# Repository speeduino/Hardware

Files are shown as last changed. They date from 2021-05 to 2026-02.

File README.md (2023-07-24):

<div align="center">

Speeduino
 
[]

##### A low cost, DIY friendly Engine Management System (ECU) based on the Arduino framework
</div>

## Speeduino
The Speeduino project is a flexible, fully featured Engine Management Systems (EMS aka ECU) based on the low cost and open source Arduino platform. It provides the hardware, firmware and software components that make up an engine management system, all provided under open licenses. With over 1000 installations, Speeduino has matured into a product that meets the needs of the hobbyist and enthusiast community without driving prices to the levels of traditional aftermarket ECUs.

## Overview
This repositiory contains the official Speeduino hardware designs. All new designs have been made in Kicad, with some early boards developed in Fritzing. 

## License
These designs are release under the [CERN Open Hardware License v2 Strong (CERN-OHL-S)](https://ohwr.org/cern_ohl_s_v2.txt). 
This license is similar to the GPL, however is designed specifically for hardware design files, including PCB layouts and schematics. As the 'strongly reciprocal' version of the CERN OHL is used, you may use, copy, modify and create variations of these designs freely, provided that any changes or variations are also released under this CERN-OHL-S. 

## Where to Buy
[Pre-made Speeduino units/boards are available from a number of official resellers](https://speeduino.com/home/where-to-buy)

These resellers all contribute a portion of sales back to the project to allow for continued development to take place and we encourage sales through them whenever possible. 
 
Of course, being open source, you are free to use the design files provided here to create your own hardware! 

## Support
In addition the manual referenced above, Speeduino has a large and very vibrant community of people to help out with your setup or any questions you might add. 

* [Speeduino Forum](https://speeduino.com/forum) 
* [Discord](hhttps://discord.com/invite/taXeNM6xNb)
* [Facebook](https://www.facebook.com/groups/191918764521976/)

## Contributors

This project exists thanks to all the people who contribute, both in terms of code and testing provided. If you'd like to get involved, please have a read through [Contributing](contributing.md) and then jump on Discord to discuss things further

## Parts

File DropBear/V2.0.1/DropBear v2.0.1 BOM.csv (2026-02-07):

Comment | Designator | Footprint | LCSC
Pololu_Breakout_DRV8825 | A1 | Module:Pololu_Breakout-16_15.2x20.3mm
Battery_Cell | BT1 | Battery:BatteryHolder_Keystone_500
0.1uF | C1,C2,C3,C9,C12,C13,C14,C21,C22,C26,C32,C34,C38 | Capacitor_SMD:C_0805_2012Metric
1uF | C10,C11,C23 | Capacitor_SMD:C_0805_2012Metric
270nF | C15,C19 | Capacitor_SMD:C_0805_2012Metric
0.22uF | C17,C18,C24,C25,C28 | Capacitor_SMD:C_0805_2012Metric
100uF | C27 | Capacitor_SMD:C_1206_3216Metric
100uF | C31 | Capacitor_SMD:CP_Elec_6.3x7.7
47uF | C33,C35 | Capacitor_Tantalum_SMD:CP_EIA-3528-21_Kemet-B
33uF | C36,C37 | Capacitor_SMD:CP_Elec_6.3x7.7
0.33uF | C39 | Capacitor_SMD:C_0805_2012Metric
0.01uF | C4,C7,C20,C29,C30 | Capacitor_SMD:C_0805_2012Metric
4700pF | C5,C16 | Capacitor_SMD:C_0805_2012Metric
1nF | C6,C8 | Capacitor_SMD:C_0805_2012Metric
D_Schottky | D1,D32 | Diode_SMD:D_PowerDI-123
D | D10,D11,D12,D13,D14,D15,D16,D17,D28,D29,D33,D34,D35,D37,D38 | Diode_SMD:D_SOD-323
LED | D2,D3,D4,D5,D6,D7,D8,D9,D18,D19,D20,D21,D22,D23,D24,D25,D31,D36,D41,D42,D43 | LED_SMD:LED_0805_2012Metric
D_TVS | D26,D27 | Diode_SMD:D_SOD-523
D_TVS | D30 | Diode_SMD:D_SOD-123F
D_TVS | D39 | Diode_SMD:D_SMB
D_Schottky | D40 | Diode_SMD:D_SMA_Handsoldering
Polyfuse | F1 | Fuse:Fuse_1812_4532Metric
Polyfuse | F2 | Fuse:Fuse_0603_1608Metric
MAX9926UAEE_V+ | IC1 | Package_SO:QSOP-16_3.9x4.9mm_P0.635mm
ZXMS6006DT8 | IC2,IC3,IC4,IC5 | IC_Automotive:Diodes_SM8
Delphi_Sicma_24 | J1 | Connector_Automotive:Delphi_Sicma_24_Grey
Delphi_Sicma_24 | J2 | Connector_Automotive:Delphi_Sicma_24_Black
EBC05DRXN | J3 | Misc:EBC05DRXN
SolderJumper_2_Bridged | JP1 | Jumper:SolderJumper-2_P1.3mm_Bridged_Pad1.0x1.5mm
Jumper_NO_Small | JP2 | Jumper:SolderJumper-2_P1.3mm_Open_Pad1.0x1.5mm
Jumper_2_Open | JP3,JP4,JP5 | Jumper:SolderJumper-2_P1.3mm_Open_Pad1.0x1.5mm
Q_DUAL_NMOS_S1G1D2S2G2D1 | Q2,Q3 | Package_TO_SOT_SMD:SOT-363_SC-70-6
470R | R1,R31,R33,R34,R38,R39,R44 | Resistor_SMD:R_0805_2012Metric
10k | R19,R20,R64 | Resistor_SMD:R_0805_2012Metric
604R | R29 | Resistor_SMD:R_0805_2012Metric
0R | R3 | Resistor_SMD:R_0805_2012Metric
3.88k | R30 | Resistor_SMD:R_0603_1608Metric_Pad0.98x0.95mm_HandSolder
2.4k | R32 | Resistor_SMD:R_0805_2012Metric
2.49k | R36,R37,R74 | Resistor_SMD:R_0805_2012Metric
120R | R4 | Resistor_SMD:R_0805_2012Metric
180k | R40,R41,R45,R46,R50,R53 | Resistor_SMD:R_0805_2012Metric
348k | R42,R43,R47,R48,R51,R54 | Resistor_SMD:R_0805_2012Metric
1k | R5,R6,R11,R12,R13,R14,R15,R16,R17,R18,R21,R22,R23,R24,R25,R26,R27,R28,R35,R49,R52,R55,R56,R57,R58,R63,R65,R66,R67,R68,R73,R75,R76 | Resistor_SMD:R_0805_2012Metric
100k | R59,R60,R61,R62,R69,R70,R71,R72 | Resistor_SMD:R_0805_2012Metric
10k | R7,R8,R9,R10 | Resistor_SMD:R_1206_3216Metric
SW_DPDT_x2 | SW1,SW2,SW4,SW5 | Misc:AYZ0202AGRLC
SW_DIP_x02 | SW3 | Button_Switch_SMD:SW_DIP_SPSTx02_Slide_9.78x7.26mm_W8.61mm_P2.54mm
Teensy4.1 | U1 | Shields:Teensy41
KP234 | U11 | Misc:KP234
LMV324LIDT | U12,U14 | Package_SO:SOIC-14_3.9x8.7mm_P1.27mm
SP720 | U13 | Package_SO:SOIC-16_3.9x9.9mm_P1.27mm
MC78M05_TO252 | U15 | Package_TO_SOT_SMD:TO-252-2
MCP2562-E-SN | U2 | Package_SO:SOIC-8_3.9x4.9mm_P1.27mm
W25Q32JVSS | U3 | Package_SO:SOIC-8_5.23x5.23mm_P1.27mm
~ | U4 | Misc:ESP32-C3 SUPERMINI
TC4424A | U5,U6,U9,U10 | Package_SO:SOIC-8_3.9x4.9mm_P1.27mm
MC33810 | U7,U8 | IC_Automotive:SOIC32-P0.65-33N

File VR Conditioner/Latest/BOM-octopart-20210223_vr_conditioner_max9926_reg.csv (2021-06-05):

Qty | Line Item | Manufacturer | MPN | Octopart URL | Schematic Reference | Internal Part Number | Description | Lifecycle Status | Lead Time | RoHS | Total Qty (@ Batch Size: 1) | SKU | SKU | SKU | SKU | Packaging | Packaging | Packaging | Packaging | Unit Price (@ Batch Size: 1) | Unit Price (@ Batch Size: 1) | Unit Price (@ Batch Size: 1) | Unit Price (@ Batch Size: 1) | In Stock | In Stock | In Stock | In Stock | MOQ | MOQ | MOQ | MOQ | URL | URL | URL | URL | Distributor [Lowest Price (Overall)] | SKU [Lowest Price (Overall)] | Packaging [Lowest Price (Overall)] | Unit Price (@ Batch Size: 1) [Lowest Price (Overall)] | Line Total [Lowest Price (Overall)] | Batch Total [Lowest Price (Overall)] | In Stock [Lowest Price (Overall)] | MOQ [Lowest Price (Overall)] | URL [Lowest Price (Overall)] | Notes
 |  |  |  |  |  |  |  |  |  |  |  | Digi-Key | Future Electronics | Mouser | RS Components | Digi-Key | Future Electronics | Mouser | RS Components | Digi-Key | Future Electronics | Mouser | RS Components | Digi-Key | Future Electronics | Mouser | RS Components | Digi-Key | Future Electronics | Mouser | RS Components | Digi-Key | Future Electronics | Mouser | RS Components
1 | GRM1857U1A103JA44D | Murata | GRM1857U1A103JA44D | https://octopart.com/grm1857u1a103ja44d-murata-17754272 |  |  |  | Production (Last Updated: 2 weeks ago) | 23w | Compliant | 1 | 490-8269-1-ND | 1117428 | 81-GRM1857U1A103JA4D |  | Cut Tape | Cut Tape | Tape & Reel |  | 0.15622662 | 0.159777225 | 0.17753025 |  | 24842 | 8000 | 6230 |  | 1 | 1 | 1 |  | https://octopart.com/click/track?country=JE&ct=offers&ppid=17754272&sid=459&sig=0a4da8a&vpid=88253296&ai4=706 | https://octopart.com/click/track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 | https://octopart.com/click/track?country=JE&ct=offers&ppid=17754272&sid=2401&sig=0942290&vpid=37708184&ai4=706 |  | Arrow Electronics | GRM1857U1A103JA44D | Cut Tape | 0.1077253557 | 0.1077253557 | 0.1077253557 | 1 | 1 | https://octopart.com/click/track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
2 | CRCW06031K00FKEAHP | Vishay | CRCW06031K00FKEAHP | https://octopart.com/crcw06031k00fkeahp-vishay-42634138 |  |  |  |  | 24w | Compliant | 2 | 541-1.00KSCT-ND | 7110920 | 71-CRCW06031K00FKEAH | 8206776 | Cut Tape | Cut Tape | Tape & Reel |  | 0.12072057000000001 | 0.104387787 | 0.12072057000000001 |  | 205723 | 16210 | 69615 | 2125 | 1 | 1 | 1 | 25 | https://octopart.com/click/track?country=JE&ct=offers&ppid=42634138&sid=459&sig=04dce86&vpid=115677389&ai4=706 | https://octopart.com/click/track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 | https://octopart.com/click/track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 | https://octopart.com/click/track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 | Farnell | 1738905 | Cut Tape | 0.0412 | 0.0824 | 0.0824 | 32145 | 1 | https://octopart.com/click/track?country=JE&ct=offers&ppid=42634138&sid=819&sig=05fe86e&vpid=250080956&ai4=706
4 | CRCW060310K0FKEAHP | Vishay | CRCW060310K0FKEAHP | https://octopart.com/crcw060310k0fkeahp-vishay-42634028 |  |  |  |  | 24w | Compliant | 4 | 541-10.0KSCT-ND | 6103726 | 71-CRCW060310K0FKEAH | 8206742 | Cut Tape | Cut Tape | Tape & Reel |  | 0.12072057000000001 | 0.104387787 | 0.12072057000000001 |  | 84206 | 65036 | 112208 | 2550 | 1 | 1 | 1 | 25 | https://octopart.com/click/track?country=JE&ct=offers&ppid=42634028&sid=459&sig=0828559&vpid=115262443&ai4=706 | https://octopart.com/click/track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 | https://octopart.com/click/track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 | https://octopart.com/click/track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 | Newark | 68R2991 | Cut Tape | 0.017753025000000002 | 0.07101210000000001 | 0.07101210000000001 | 10760 | 1 | https://octopart.com/click/track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
1 | MAX9926UAEE+ | Maxim Integrated | MAX9926UAEE+ | https://octopart.com/max9926uaee%2B-maxim+integrated-42513566 |  |  |  | Production (Last Updated: 1 month ago) | 6w | Compliant | 1 | MAX9926UAEE+-ND | 3086399 | 700-MAX9926UAEE | 1901381 | Tube | Tube | Tube |  | 4.86432885 |  | 6.44789868 | 4.98 | 1069 | 100 | 299 | 0 | 1 | 100 | 1 | 1 | https://octopart.com/click/track?country=JE&ct=offers&ppid=42513566&sid=459&sig=0fd0a9b&vpid=115650128&ai4=706 | https://octopart.com/click/track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 | https://octopart.com/click/track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 | https://octopart.com/click/track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 | Newark | 73Y6635 |  | 4.73650707 | 4.73650707 | 4.73650707 | 10 | 1 | https://octopart.com/click/track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
1 | GCM188R71C105KA64D | Murata | GCM188R71C105KA64D | https://octopart.com/gcm188r71c105ka64d-murata-13159598 |  |  |  | Production (Last Updated: 2 weeks ago) | 27w | Compliant | 1 | 490-5241-1-ND | 7025260 | 81-GCM188R71C105K64D | 7900562 | Cut Tape | Cut Tape | Tape & Reel |  | 0.15622662 | 0.152676015 | 0.15622662 |  | 272359 | 2118 | 0 | 11400 | 1 | 1 | 1 | 25 | https://octopart.com/click/track?country=JE&ct=offers&ppid=13159598&sid=459&sig=065a155&vpid=34232850&ai4=706 | https://octopart.com/click/track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 | https://octopart.com/click/track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 | https://octopart.com/click/track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 | Arrow Electronics | GCM188R71C105KA64D | Cut Tape | 0.1297391067 | 0.1297391067 | 0.1297391067 | 52386 | 1 | https://octopart.com/click/track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
1 | GRM21BR61E106MA73L | Murata | GRM21BR61E106MA73L | https://octopart.com/grm21br61e106ma73l-murata-46693545 |  |  |  | Production (Last Updated: 2 weeks ago) | 29w | Compliant | 1 | 490-10748-1-ND | 3104124 | 81-GRM21BR61E106MA3L | 1726799 | Cut Tape | Cut Tape | Tape & Reel |  | 0.17753025 | 0.173979645 | 0.18463146 |  | 169134 | 22568 | 63443 | 700 | 1 | 1 | 1 | 50 | https://octopart.com/click/track?country=JE&ct=offers&ppid=46693545&sid=459&sig=0e7381d&vpid=210890997&ai4=706 | https://octopart.com/click/track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 | https://octopart.com/click/track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 | https://octopart.com/click/track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 | Arrow Electronics | GRM21BR61E106MA73L | Cut Tape | 0.1290289857 | 0.1290289857 | 0.1290289857 | 18282 | 1 | https://octopart.com/click/track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
2 | GRM1885C1H102JA01D | Murata | GRM1885C1H102JA01D | https://octopart.com/grm1885c1h102ja01d-murata-196169 |  |  |  | Production (Last Updated: 2 weeks ago) | 29w | Compliant | 2 | 490-1451-1-ND | 5104092 | 81-GRM39C102J50 | 7235795 | Cut Tape | Cut Tape | Tape & Reel |  | 0.07101210000000001 | 0.0102257424 | 0.07101210000000001 |  | 0 | 2890 | 845260 | 5800 | 1 | 1 | 1 | 200 | https://octopart.com/click/track?c=1&country=JE&ct=offers&ppid=196169&sid=459&sig=0c67cea&vpid=1086114&ai4=706 | https://octopart.com/click/track?country=JE&ct=offers&ppid=196169&sid=2454&sig=06c4930&vpid=495870445&ai4=706 | https://octopart.com/click/track?country=JE&ct=offers&ppid=196169&sid=2401&sig=0c58fdf&vpid=37712468&ai4=706 | https://octopart.com/click/track?country=JE&ct=offers&ppid=196169&sid=10022&sig=0888f0c&vpid=199072014&ai4=706 | Future Electronics | 5104092 | Cut Tape | 0.0102257424 | 0.0204514848 | 0.0204514848 | 2890 | 1 | https://octopart.com/click/track?country=JE&ct=offers&ppid=196169&sid=2454&sig=06c4930&vpid=495870445&ai4=706
1 | GCJ188R71C104KA01D | Murata | GCJ188R71C104KA01D | https://octopart.com/gcj188r71c104ka01d-murata-21222040 |  |  |  | Production (Last Updated: 2 weeks ago) | 27w | Compliant | 1 | 490-5796-1-ND | 6113232 | 81-GCJ188R71C104KA1D |  | Cut Tape | Cut Tape | Tape & Reel |  | 0.19173267000000002 | 0.188182065 | 0.17042904 |  | 38484 | 1000 | 178383 |  | 1 | 1 | 1 |  | https://octopart.com/click/track?country=JE&ct=offers&ppid=21222040&sid=459&sig=0e464ea&vpid=44469513&ai4=706 | https://octopart.com/click/track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 | https://octopart.com/click/track?country=JE&ct=offers&ppid=21222040&sid=2401&sig=02bb046&vpid=47654983&ai4=706 |  | Mouser | 81-GCJ188R71C104KA1D | Tape & Reel | 0.17042904 | 0.17042904 | 0.17042904 | 178383 | 1 | https://octopart.com/click/track?country=JE&ct=offers&ppid=21222040&sid=2401&sig=02bb046&vpid=47654983&ai4=706

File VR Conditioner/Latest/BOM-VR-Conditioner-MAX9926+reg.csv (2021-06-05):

Reference | Value | Footprint | Datasheet | Critical | Description | MFG Name | MFG Part Num | Package JEDEC ID
FID1 | Fiducial | Fiducial:Fiducial_0.5mm_Mask1mm | ~
FID2 | Fiducial | Fiducial:Fiducial_0.5mm_Mask1mm | ~
U1 | MAX9926UAEE+ | MAX9926UAEE+:MAX9926UAEE&plus_ | https://datasheet.octopart.com/MAX9926UAEE%2B-Maxim-Integrated-datasheet-11046290.pdf | Yes | MAX9926 Series 10 mA Differential Input Logic Output Sensor Interface -SSOP-16 | Maxim Integrated | MAX9926UAEE+ | SSOP-16
C1 | 10n | Capacitor_SMD:C_0603_1608Metric | ~ |  | 10 V ±5% Tolerance U2J Multilayer Ceramic Capacitor | Murata Murata | GRM1857U1A103JA44D | 0603_1608Metric
C2 | 100n | Capacitor_SMD:C_0603_1608Metric | ~ |  | Ceramic 0.1uF 16V X7R 10% Pad SMD 0603 Soft Termination 125C Automotive T/R | Murata | GCJ188R71C104KA01D | 0603_1608Metric
C3 | 1u | Capacitor_SMD:C_0603_1608Metric | ~ |  | 16V ±10% Tolerance X7R Surface Mount Multilayer Ceramic Capacitor | Murata | GCM188R71C105KA64D | 0603_1608Metric
C20 | 1n | Capacitor_SMD:C_0603_1608Metric | ~ |  | 1000 pF 50 V ±5 % Tolerance C0G SMT Multilayer Ceramic Capacitor | Murata | GRM1885C1H102JA01D | 0603_1608Metric
C10 | 1n | Capacitor_SMD:C_0603_1608Metric | ~ |  | 1000 pF 50 V ±5 % Tolerance C0G SMT Multilayer Ceramic Capacitor | Murata | GRM1885C1H102JA01D | 0603_1608Metric
R22 | 10k | Resistor_SMD:R_0603_1608Metric_Pad1.05x0.95mm_HandSolder | ~ |  |  | Yageo | RC1206FR-7W10KL | Resistor_SMD:R_1206_3216Metric
R21 | 10k | Resistor_SMD:R_0603_1608Metric_Pad1.05x0.95mm_HandSolder | ~ |  |  | Yageo | RC1206FR-7W10KL | Resistor_SMD:R_1206_3216Metric
R11 | 10k | Resistor_SMD:R_0603_1608Metric_Pad1.05x0.95mm_HandSolder | ~ |  |  | Yageo | RC1206FR-7W10KL | Resistor_SMD:R_1206_3216Metric
R12 | 10k | Resistor_SMD:R_0603_1608Metric_Pad1.05x0.95mm_HandSolder | ~ |  |  | Yageo | RC1206FR-7W10KL | Resistor_SMD:R_1206_3216Metric
R13 | 4.7k | Resistor_THT:R_Axial_DIN0207_L6.3mm_D2.5mm_P7.62mm_Horizontal | ~ | DoNoPlace. User option | 3W, 5%
J1 | 8-pin header | Package_DIP:DIP-8_W7.62mm | ~
R20 | 1k | Resistor_SMD:R_0603_1608Metric_Pad1.05x0.95mm_HandSolder | ~ |  | Thick Film; +/-1% 0.2W | Vishay | CRCW06031K00FKEAHP | 0603_1608Metric
R10 | 1k | Resistor_SMD:R_0603_1608Metric_Pad1.05x0.95mm_HandSolder | ~ |  | Thick Film; +/-1% 0.2W | Vishay | CRCW06031K00FKEAHP | 0603_1608Metric
H1 | MountingHole | MountingHole:MountingHole_2.2mm_M2 | ~
H2 | MountingHole | MountingHole:MountingHole_2.2mm_M2 | ~
C4 | 10u | Capacitor_SMD:C_0805_2012Metric | ~ |  | 25 V 10 uF ±20% Tolerance X5R Multilayer Ceramic Capacitor | Murata | GRM21BR61E106MA73L | 0805_2012Metric
R23 | 4.7k | Resistor_THT:R_Axial_DIN0207_L6.3mm_D2.5mm_P7.62mm_Horizontal | ~ | DoNoPlace. User option | 3W, 5%
U2 | AMS1117CD-5.0 | Package_TO_SOT_THT:TO-92_Inline_Wide | http://www.advanced-monolithic.com/pdf/ds1117.pdf | DoNoPlace. User option | 1A Low Dropout Voltage Regulator | Advanced Monolithic Systems | AMS1117-5.0 | TO92 inline wide
J2 | Edge | Connector_PinHeader_2.54mm:PinHeader_1x04_P2.54mm_Horizontal | ~ | DoNoPlace. User option

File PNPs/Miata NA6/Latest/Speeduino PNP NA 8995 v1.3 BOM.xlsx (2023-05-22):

Reference | Quantity | Value | Footprint | Manufacturer_Name | Manufacturer_Part_Number | URL | Digikey Part Number
C1 C29 | 2 | 0.01uF | Capacitor_SMD:C_0805_2012Metric | Yageo | CC0805KRX7R9BB103 | https://www.digikey.com/product-detail/en/yageo/CC0805KRX7R9BB103/311-1136-1-ND/303046 | 311-1136-1-ND
C17 | 1 | 22uF | Capacitor_SMD:CP_Elec_4x5.8 | Panasonic | EEE-FK0J220R | https://www.digikey.com/product-detail/en/panasonic-electronic-components/EEE-FK0J220R/PCE3765CT-ND/766141 | PCE3765CT-ND
C19 | 1 | 10uF | Capacitor_Tantalum_SMD:CP_EIA-7343-31_Kemet-D | Kemet | T491D106K050AT | https://www.digikey.com/product-detail/en/kemet/T491D106K050AT/399-8361-1-ND/3472084 | 399-8361-1-ND
C2 C30 C18 | 3 | 1uF | Capacitor_SMD:C_0805_2012Metric | Yageo | CC0805KKX7R7BB105 | https://www.digikey.com/product-detail/en/yageo/CC0805KKX7R7BB105/311-1365-1-ND/2103149 | 311-1365-1-ND
C20 C22 C23 | 3 | 0.1uF | Capacitor_SMD:C_1206_3216Metric | Kemet | C1206C104K5RAC7867 | https://www.digikey.com/product-detail/en/kemet/C1206C104K5RAC7867/399-1249-1-ND/411524 | 399-1249-1-ND
C21 | 1 | 22uF | Capacitor_SMD:C_0805_2012Metric_Pad1.15x1.40mm_HandSolder | Samsung | CL21A226KQCLRNC | https://www.digikey.com.au/product-detail/en/samsung-electro-mechanics/CL21A226KQCLRNC/1276-6687-1-ND/5961546 | 1276-6687-1-ND
C24 C25 | 2 | 47uF | Capacitor_Tantalum_SMD:CP_EIA-3528-21_Kemet-B | AVX | TAJB476K006RNJ | https://www.digikey.com/product-detail/en/avx-corporation/TAJB476K006RNJ/478-1692-1-ND/564724 | 478-1692-1-ND
C32 | 1 | 0.1uF | Capacitor_SMD:C_0805_2012Metric_Pad1.15x1.40mm_HandSolder | Yageo | CC0805KRX7R9BB104 | https://www.digikey.com.au/product-detail/en/yageo/CC0805KRX7R9BB104/311-1140-1-ND/303050 | 311-1140-1-ND
C33 C3 C9 C10 C11 C4 C15 C16 C31 C27 C26 C28 | 12 | 0.1uF | Capacitor_SMD:C_0805_2012Metric | Yageo | CC0805KRX7R9BB104 | https://www.digikey.com.au/product-detail/en/yageo/CC0805KRX7R9BB104/311-1140-1-ND/303050 | 311-1140-1-ND
C5 | 1 | 0.27uF | Capacitor_SMD:C_0805_2012Metric | Yageo | CC0805JRX7R7BB274 | https://www.digikey.com.au/product-detail/en/yageo/CC0805JRX7R7BB274/311-4268-1-ND/8025357 | 311-4268-1-ND
C6 C12 C13 C14 C7 | 5 | 0.22uF | Capacitor_SMD:C_0805_2012Metric | Samsung | CL21B224KOCNNNC | https://www.digikey.com/product-detail/en/samsung-electro-mechanics-america-inc/CL21B224KOCNNNC/1276-1284-1-ND/3889370 | 1276-1284-1-ND
C8 | 1 | 470pf | Capacitor_SMD:C_0805_2012Metric | Yageo | CC0805KRX7R9BB471 | https://www.digikey.com/product-detail/en/yageo/CC0805KRX7R9BB471/311-1124-1-ND/303034 | 311-1124-1-ND
D10 D9 D5 D6 D20 | 5 | D | Diode_SMD:D_SOD-323 | Micro Commercial Co | 1N4448WX-TP | https://www.digikey.com/product-detail/en/micro-commercial-co/1N4448WX-TP/1N4448WXTPMSCT-ND/789338 | 1N4448WXTPMSCT-ND
D12 | 1 | D_Schottky | Diode_THT:D_DO-41_SOD81_P7.62mm_Horizontal | Micro Commercial Co | 1N5818-TP | https://www.digikey.com/product-detail/en/micro-commercial-co/1N5818-TP/1N5818-TPCT-ND/950587 | 1N5818-TPCT-ND
D16 D15 D17 | 3 | D | Diode_SMD:D_SMB | ON Semi | NBRS2H100T3G | https://www.digikey.com/en/products/detail/on-semiconductor/NBRS2H100T3G/1792405 | NBRS2H100T3GTR-ND
D22 D21 | 2 | LED_Green | LED_SMD:LED_0805_2012Metric | Osram | LG R971-KN-1 | https://www.digikey.com/product-detail/en/osram-opto-semiconductors-inc/LG-R971-KN-1/475-1410-1-ND/1802598 | 475-1410-1-ND
D23 | 1 | D_TVS | Diode_SMD:D_SMB | Bournes Inc. | SMBJ40A-Q | https://www.digikey.com.au/product-detail/en/bourns-inc/SMBJ40A-Q/SMBJ40A-QCT-ND/10222718 | SMBJ40A-QCT-ND
D4 D3 D8 D7 D1 D2 D11 D19 D18 | 9 | LED | LED_SMD:LED_0805_2012Metric | Osram | LH R974-LP-1 | https://www.digikey.com/product-detail/en/osram-opto-semiconductors-inc/LH-R974-LP-1/475-1415-1-ND/1802604 | 475-1415-1-ND
F1 | 1 | Polyfuse | Fuse:Fuse_0603_1608Metric | Bel Fuse | 0ZCM0008FF2G | https://www.digikey.com.au/product-detail/en/bel-fuse-inc/0ZCM0008FF2G/507-1817-1-ND/4156262 | 507-1817-1-ND
J1 | 1 | 174917-1 | Connector_Automotive:1749171 | TE Connectivity | 174917-1
Q1 | 1 | Q_PNP_BCEC | Package_TO_SOT_SMD:SOT-223-3_TabPin2 | Diodes Inc | FZT753TA | https://www.digikey.com.au/product-detail/en/diodes-incorporated/FZT753TA/FZT753CT-ND/92847 | FZT753CT-ND
R1 R2 R15 R16 R3 R4 R56 R57 R42 R41 R51 R50 R47 | 13 | 100k | Resistor_SMD:R_0805_2012Metric_Pad1.15x1.40mm_HandSolder | Yageo | RC0805FR-07100KL | https://www.digikey.com/product-detail/en/yageo/RC0805FR-07100KL/311-100KCRCT-ND/730491 | 311-100KCRCT-ND
R10 R9 R20 R19 R11 R12 R60 R61 R25 | 9 | 2.4k | Resistor_SMD:R_0805_2012Metric | Yageo | RC0805FR-072K4L | https://www.digikey.com/product-detail/en/yageo/RC0805FR-072K4L/311-2.40KCRCT-ND/730637 | 311-2.40KCRCT-ND
R22 | 1 | 3.9k | Resistor_SMD:R_0805_2012Metric | Yageo | RC0805FR-073K9L | https://www.digikey.com/product-detail/en/yageo/RC0805FR-073K9L/311-3.90KCRCT-ND/730785 | 311-3.90KCRCT-ND
R26 R23 R30 R31 R32 R24 R66 R65 R55 R54 | 10 | 470R | Resistor_SMD:R_0805_2012Metric | Panasonic | ERJ-6ENF4700V | https://www.digikey.com/product-detail/en/panasonic-electronic-components/ERJ-6ENF4700V/P470CCT-ND/1746871 | P470CCT-ND
R27 R28 R52 | 3 | 2.49k | Resistor_SMD:R_0805_2012Metric | Yageo | RT0805BRD072K49L | https://www.digikey.com/product-detail/en/yageo/RT0805BRD072K49L/YAG1854CT-ND/5139302 | YAG1854CT-ND
R35 R36 | 2 | 220R | Resistor_SMD:R_0805_2012Metric_Pad1.15x1.40mm_HandSolder | Yageo | RC0805FR-07220RL | https://www.digikey.com/product-detail/en/yageo/RC0805FR-07220RL/311-220CRCT-ND/730688 | 311-220CRCT-ND
R37 | 1 | 10k | Resistor_SMD:R_0805_2012Metric | Yageo | RC0805JR-0710KL | https://www.digikey.com/product-detail/en/yageo/RC0805JR-0710KL/311-10KARCT-ND/731188 | 311-10KARCT-ND
R38 | 1 | 120R | Resistor_SMD:R_0805_2012Metric | Yageo | RC0805FR-07120RL | https://www.digikey.com/product-detail/en/yageo/RC0805FR-07120RL/311-120CRCT-ND/730522 | 311-120CRCT-ND
R43 | 1 | 2k | Resistor_SMD:R_0805_2012Metric_Pad1.15x1.40mm_HandSolder | Yageo | RC0805FR-072KL | https://www.digikey.com/product-detail/en/yageo/RC0805FR-072KL/311-2.00KCRCT-ND/730611 | 311-2.00KCRCT-ND
R46 | 1 | 10k | Resistor_SMD:R_0805_2012Metric_Pad1.15x1.40mm_HandSolder | Yageo | RC0805JR-0710KL |  | 311-10KARCT-ND
R5 R6 R17 R18 R7 R8 R58 R59 R21 R29 R33 R34 R39 R40 R48 R49 R44 R45 R53 R64 | 20 | 1k | Resistor_SMD:R_0805_2012Metric_Pad1.15x1.40mm_HandSolder | Yageo | RC0805FR-071KL | https://www.digikey.com/product-detail/en/yageo/RC0805FR-071KL/311-1.00KCRCT-ND/730391 | 311-1.00KCRCT-ND
R67 | 1 | 22K | Resistor_SMD:R_0805_2012Metric | Yageo | AC0805JR-0722KL | https://www.digikey.com.au/product-detail/en/yageo/AC0805JR-0722KL/YAG3773CT-ND/6006622 | YAG3773CT-ND
RV1 | 1 | Varistor | Varistor:RV_Disc_D15.5mm_W4.7mm_P7.5mm | Bourns Inc | MOV-14D220K | https://www.digikey.com.au/product-detail/en/bourns-inc/MOV-14D220K/MOV-14D220K-ND/2799109 | MOV-14D220K-ND
S1 | 1 | AYZ0202AGRLC | AYZ0202AGRLC | C & K COMPONENTS | AYZ0202AGRLC | https://www.digikey.com.au/product-detail/en/c-k/AYZ0202AGRLC/401-2013-1-ND/1640122 | 401-2013-1-ND
U1 | 1 | MC33814 | Package_QFP:LQFP-48-1EP_7x7mm_P0.5mm_EP3.6x3.6mm_ThermalVias | NCP | MC33814 | http://au.element14.com/nxp/mc33814ae/ic-control-1-cylinder-engine-48lqfp/dp/2311285
U11 | 1 | KP234 | Misc:KP234 | Infineon | KP234XTMA1 | https://www.digikey.com.au/product-detail/en/infineon-technologies/KP234XTMA1/448-KP234XTMA1CT-ND/12718428 | 448-KP234XTMA1CT-ND
U2 U4 U7 U9 | 4 | VNLD5090 | Package_SO:SO-8_3.9x4.9mm_P1.27mm | STMicro | VNLD5090-E | https://mouser.com/search/ProductDetail.aspx?R=0virtualkey0virtualkeyVNLD5090-E | 497-18682-ND
U3 U10 | 2 | TC4424A | Package_SO:SOIC-8_3.9x4.9mm_P1.27mm | Microchip | TC4424AVOA | https://www.digikey.com/product-detail/en/microchip-technology/TC4424AVOA/TC4424AVOA-ND/1098908 | TC4424AVOA-ND
U5 | 1 | MPX4250 | Misc:MPX4250 | NXP | MPX4250AP | https://www.digikey.com.au/product-detail/en/nxp-usa-inc/MPX4250AP/MPX4250AP-ND/464053 | MPX4250AP-ND
U6 | 1 | SP720 | Package_SO:SOIC-16_3.9x9.9mm_P1.27mm | Littelfuse | SP720ABTG | https://www.digikey.com/product-detail/en/littelfuse-inc/SP720ABTG/F3162CT-ND/1984458 | F3162CT-ND
U8 | 1 | VN5160S-E | Package_SO:SO-8_3.9x4.9mm_P1.27mm | STMicro | VN5160S-E | https://www.digikey.com.au/products/en?keywords=VN5160S-E | 497-19720-ND
XA1 | 4 | Arduino_Mega2560 header pins | CONN HEADER .100" SNGL STR 40POS | Sullins Connector Solutions | PREC040SAAN-RC | https://www.digikey.com.au/products/en?keywords=S1012EC-40-ND |  | Pins attach to bottom of board

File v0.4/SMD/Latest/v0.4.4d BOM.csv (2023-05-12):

Reference | Quantity | Value | Footprint | Manufacturer_Name | Manufacturer_Part_Number | URL | Part # | Voltage | Allied_Number | Description | RS Part Number | RS Price/Stock | TR PN | Tube PN | Spice_Model | Spice_Netlist_Enabled | Spice_Primitive
C1 C15 | 2 | 0.01uF | Capacitor_SMD:C_0805_2012Metric | Yageo | CC0805KRX7R9BB103 | https://www.digikey.com/product-detail/en/yageo/CC0805KRX7R9BB103/311-1136-1-ND/303046
C17 | 1 | 10uF | Capacitor_Tantalum_SMD:CP_EIA-7343-31_Kemet-D | Kemet | T491D106K050AT | https://www.digikey.com/product-detail/en/kemet/T491D106K050AT/399-8361-1-ND/3472084 |  | 35v
C19 | 1 | 22uF | Capacitor_SMD:C_0805_2012Metric_Pad1.15x1.40mm_HandSolder | Samsung | CL21A226KQCLRNC | https://www.digikey.com.au/product-detail/en/samsung-electro-mechanics/CL21A226KQCLRNC/1276-6687-1-ND/5961546
C21 | 1 | 47uF | Capacitor_Tantalum_SMD:CP_EIA-3528-21_Kemet-B | AVX | TAJB476K006RNJ | https://www.digikey.com/product-detail/en/avx-corporation/TAJB476K006RNJ/478-1692-1-ND/564724 |  | 10v
C24 C26 C3 C9 C10 C11 C4 C16 C18 C20 C23 C22 C28 | 13 | 0.1uF | Capacitor_SMD:C_0805_2012Metric | Yageo | CC0805KRX7R9BB104 | https://www.digikey.com.au/product-detail/en/yageo/CC0805KRX7R9BB104/311-1140-1-ND/303050
C25 C27 C2 | 3 | 1uF | Capacitor_SMD:C_0805_2012Metric | Yageo | CC0805KKX7R7BB105 | https://www.digikey.com/product-detail/en/yageo/CC0805KKX7R7BB105/311-1365-1-ND/2103149
C6 C12 C13 C14 C7 C5 | 6 | 0.22uF | Capacitor_SMD:C_0805_2012Metric | Samsung | CL21B224KOCNNNC | https://www.digikey.com/product-detail/en/samsung-electro-mechanics-america-inc/CL21B224KOCNNNC/1276-1284-1-ND/3889370
C8 C29 | 2 | 470pf | Capacitor_SMD:C_0805_2012Metric | Yageo | CC0805KRX7R9BB471 | https://www.digikey.com/product-detail/en/yageo/CC0805KRX7R9BB471/311-1124-1-ND/303034
D12 D11 D5 D6 | 4 | D | Diode_SMD:D_SOD-323 | MCC | 1N4448WX-TP | https://www.digikey.com/product-detail/en/micro-commercial-co/1N4448WX-TP/1N4448WXTPMSCT-ND/789338
D13 D20 | 2 | D_Zener | Diode_SMD:D_SOD-323 | On Semi | MM3Z5V1ST1G | https://www.digikey.com/product-detail/en/on-semiconductor/MM3Z5V1ST1G/MM3Z5V1ST1GOSCT-ND/964547 | MM3Z5V1ST1G
D14 | 1 | B130-13-F | Diode_SMD:D_SMA | Diodes Inc | B130-13-F | https://www.digikey.com.au/product-detail/en/diodes-incorporated/B130-13-F/B130-FDICT-ND/815318
D15 | 1 | D_TVS | Diode_SMD:D_SMB | Bournes Inc. | SMBJ40A-Q | https://www.digikey.com.au/product-detail/en/bourns-inc/SMBJ40A-Q/SMBJ40A-QCT-ND/10222718
D19 D16 D17 D18 | 4 | D | Diode_SMD:D_SOD-123F | ONSEMI | S110FA | https://www.digikey.com/en/products/detail/on-semiconductor/S110FA/5892098
D4 D3 D8 D7 D1 D2 D9 D10 | 8 | LED | LED_SMD:LED_0805_2012Metric | Osram | LH R974-LP-1 | https://www.digikey.com/product-detail/en/osram-opto-semiconductors-inc/LH-R974-LP-1/475-1415-1-ND/1802604
F1 F2 | 2 | Polyfuse | Fuse:Fuse_1812_4532Metric | Bel Fuse | 0ZCC0050FF2C | https://www.digikey.com.au/product-detail/en/bel-fuse-inc/0ZCC0050FF2C/507-1361-1-ND/1560228
IC3 | 2 | Trig Cond Socket | Package_DIP:DIP-8_W7.62mm_Socket | Sullins Connector Solutions | PPTC041LFBN-RC | https://www.digikey.com.au/product-detail/en/sullins-connector-solutions/PPTC041LFBN-RC/S7002-ND/810144
J3 | 1 | Conn_01x02 | TerminalBlock_Phoenix:TerminalBlock_Phoenix_PT-1,5-2-5.0-H_1x02_P5.00mm_Horizontal | TE | 282836-2 | https://www.digikey.com.au/product-detail/en/te-connectivity-amp-connectors/282836-2/A98076-ND/1826939
J4 | 1 | Conn_02x20_Counter_Clockwise | Connector_IDC:IDC-Header_2x20_P2.54mm_Vertical | CNC Tech | 571-5103308-8 | https://www.digikey.com.au/products/en?keywords=1175-1614-ND
JP1 | 1 | Ignition Voltage | Connector_PinHeader_2.54mm:PinHeader_1x03_P2.54mm_Vertical | Harwin Inc | M20-9990345 | https://www.digikey.com.au/products/en?keywords=M20-9990345
JP2 JP3 | 2 | VR-HALL | Connector_PinHeader_2.54mm:PinHeader_1x03_P2.54mm_Vertical | Harwin Inc | M20-9990345 | https://www.digikey.com.au/products/en?keywords=M20-9990345
JP5 JP4 | 2 | PULL-UP | Connector_PinHeader_2.54mm:PinHeader_1x02_P2.54mm_Vertical | Harwin Inc | M20-9990245 | https://www.digikey.com.au/products/en?keywords=M20-9990245
Q1 Q3 Q2 | 3 | SSM3K357R | Package_TO_SOT_SMD:SOT-23 | Toshiba | SSM3K357R | https://www.digikey.com.au/product-detail/en/toshiba-semiconductor-and-storage/SSM3K357RLF/SSM3K357RLFCT-ND/8611183
R1 R2 R15 R16 R3 R4 R19 R20 R50 R49 R61 R60 | 12 | 100k | Resistor_SMD:R_0805_2012Metric | Yageo | RC0805FR-07100KL | https://www.digikey.com/product-detail/en/yageo/RC0805FR-07100KL/311-100KCRCT-ND/730491
R10 R9 R24 R23 R11 R12 R25 R26 R33 | 9 | 2.4k | Resistor_SMD:R_0805_2012Metric | Yageo | RC0805FR-072K4L | https://www.digikey.com/product-detail/en/yageo/RC0805FR-072K4L/311-2.40KCRCT-ND/730637
R27 R28 R13 R14 | 4 | 10R | Resistor_SMD:R_1206_3216Metric | Yageo | RC1206FR-0710RL | https://www.digikey.com/en/products/detail/yageo/RC1206FR-0710RL/728482
R30 | 1 | 3.9k | Resistor_SMD:R_0805_2012Metric | Yageo | RC0805FR-073K9L | https://www.digikey.com/product-detail/en/yageo/RC0805FR-073K9L/311-3.90KCRCT-ND/730785
R34 R31 R38 R39 R40 R32 R55 R63 R62 | 9 | 470R | Resistor_SMD:R_0805_2012Metric | Panasonic | ERJ-6ENF4700V | https://www.digikey.com/product-detail/en/panasonic-electronic-components/ERJ-6ENF4700V/P470CCT-ND/1746871
R35 R36 | 2 | 2.49k | Resistor_SMD:R_0805_2012Metric | Yageo | RT0805BRD072K49L | https://www.digikey.com/product-detail/en/yageo/RT0805BRD072K49L/YAG1854CT-ND/5139302
R43 R44 | 2 | 220R | Resistor_SMD:R_0805_2012Metric | Yageo | RC0805FR-07220RL | https://www.digikey.com/product-detail/en/yageo/RC0805FR-07220RL/311-220CRCT-ND/730688
R45 R51 | 2 | 10k | Resistor_SMD:R_0805_2012Metric | Yageo | RC0805JR-0710KL | https://www.digikey.com/product-detail/en/yageo/RC0805JR-0710KL/311-10KARCT-ND/731188
R46 | 1 | 120R | Resistor_SMD:R_0805_2012Metric | Yageo | RC0805FR-07120RL | https://www.digikey.com/product-detail/en/yageo/RC0805FR-07120RL/311-120CRCT-ND/730522
R5 R6 R17 R18 R7 R8 R21 R22 R29 R37 R41 R42 R47 R48 R56 R57 R53 R54 | 18 | 1k | Resistor_SMD:R_0805_2012Metric | Yageo | RC0805FR-071KL | https://www.digikey.com/product-detail/en/yageo/RC0805FR-071KL/311-1.00KCRCT-ND/730391
R52 | 1 | 2k | Resistor_SMD:R_0805_2012Metric | Yageo | RC0805FR-072KL | https://www.digikey.com/product-detail/en/yageo/RC0805FR-072KL/311-2.00KCRCT-ND/730611
S1 | 1 | AYZ0202AGRLC | Misc:AYZ0202AGRLC | C & K COMPONENTS | AYZ0202AGRLC | https://www.digikey.com.au/product-detail/en/c-k/AYZ0202AGRLC/401-2013-1-ND/1640122 |  |  | 70417470 | AYZ0202AGRLC (Slide Switches) | 7931504P | http://uk.rs-online.com/web/p/products/7931504P
U1 U3 U7 U9 | 4 | VNLD5090 | Package_SO:SOIC-8_3.9x4.9mm_P1.27mm | STMicro | VNLD5090-E | https://www.digikey.com.au/products/en?keywords=VNLD5090-E
U2 U4 | 2 | IXDN602 | Package_SO:SOIC-8_3.9x4.9mm_P1.27mm | IXYS | IXDN602SIATR | https://www.digikey.com/en/products/detail/ixys-integrated-circuits-division/IXDN602SIATR/2424695
U5 | 1 | MPX4250 | Misc:MPX4250 | NXP | MPX4250AP | https://www.digikey.com.au/product-detail/en/nxp-usa-inc/MPX4250AP/MPX4250AP-ND/464053
U6 | 1 | SP720 | Package_SO:SOIC-16_3.9x9.9mm_P1.27mm | Littelfuse | SP720ABTG | https://www.digikey.com/product-detail/en/littelfuse-inc/SP720ABTG/F3162CT-ND/1984458
U8 | 1 | LM2940S-5.0/NOPB | Package_TO_SOT_SMD:TO-263-3_TabPin2 | TI | LM2940S-5.0/NOPB | https://www.digikey.com.au/products/en?keywords=LM2940S-5.0%2FNOPB |  |  |  |  |  |  | LM2940SX-5.0/NOPB | LM2940S-5.0/NOPB
XA1 | 4 | Arduino_Mega2560 header pins | CONN HEADER .100" SNGL STR 40POS | Sullins Connector Solutions | PREC040SAAN-RC | https://www.digikey.com.au/products/en?keywords=S1012EC-40-ND | Pins on underside of board

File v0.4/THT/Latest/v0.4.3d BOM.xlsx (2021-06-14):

 | Speeduino BOM |  |  | v0.4.3d
Reference | Quantity | Value | Manufacturer_Name | Manufacturer_Part_Number | Footprint | URL | Digikey Part Number | Digikey BOM import
A1 | 2 | DRV8825 socket | Sullins | PPTC081LFBN-RC | Module:Pololu_Breakout-16_15.2x20.3mm | https://www.digikey.com.au/products/en?keywords=PPTC081LFBN-RC | S7006-ND | 2,S7006-ND
C1 C15 | 2 | 0.01uF | TDK | FA18X7R1H103KNU06 | Capacitor_THT:C_Disc_D5.0mm_W2.5mm_P2.50mm | https://www.digikey.com.au/product-detail/en/tdk-corporation/FA18X7R1H103KNU06/445-174244-1-ND/5865002 | 445-174244-1-ND | 2,445-174244-1-ND
C17 | 1 | 10uF | Panasonic | EEU-FC1H100L | Capacitor_THT:CP_Radial_D5.0mm_P2.00mm | https://www.digikey.com.au/product-detail/en/panasonic-electronic-components/EEU-FC1H100L/P10316-ND/266325 | P10316-ND | 1,P10316-ND
C19 | 1 | 22uF | TDK | FA22X7R1E226MRU06 | Capacitor_THT:C_Disc_D7.5mm_W5.0mm_P5.00mm |  | 445-180603-1-ND | 1,445-180603-1-ND
C21 | 1 | 47uF | Panasonic | EEU-FC1H470B | Capacitor_THT:CP_Radial_D8.0mm_P5.00mm |  | P19658CT-ND | 1,P19658CT-ND
C3 C4 C9 C10 C11 C16 C18 C20 C22 C23 C24 C28 | 12 | 0.1uF | TDK | FA18X8R1E104KNU06 | Capacitor_THT:C_Disc_D5.0mm_W2.5mm_P2.50mm | https://www.digikey.com.au/product-detail/en/tdk-corporation/FA18X8R1E104KNU06/445-180563-1-ND/9560689 | 445-180563-1-ND | 12,445-180563-1-ND
C2 C25 | 2 | 1uF | TDK | FA18X7R1E105KRU06 | Capacitor_THT:C_Disc_D5.0mm_W2.5mm_P2.50mm | https://www.digikey.com.au/product-detail/en/tdk-corporation/FA18X7R1E105KRU06/445-180543-1-ND/9560669 | 445-180543-1-ND | 2,445-180543-1-ND
C5 C6 C7 C12 C13 C14 | 6 | 0.22uF | TDK | FA18X8R1E224KRU06 | Capacitor_THT:C_Disc_D5.0mm_W2.5mm_P2.50mm | https://www.digikey.com.au/product-detail/en/tdk-corporation/FA18X8R1E224KRU06/445-180564-1-ND/9560690 | 445-180564-1-ND | 6,445-180564-1-ND
C8 C29 | 2 | 470pf | TDK | FA18NP01H471JNU06 | Capacitor_THT:C_Disc_D5.0mm_W2.5mm_P2.50mm | https://www.digikey.com.au/product-detail/en/tdk-corporation/FA18NP01H471JNU06/445-180522-1-ND/9560648 | 445-180522-1-ND | 2,445-180522-1-ND
D5 D6 D11 D12 D13 D16 | 6 | Diode - General purpose | Vishay | 1N914TAP | Diode_THT:D_DO-35_SOD27_P7.62mm_Horizontal | https://www.digikey.com.au/product-detail/en/vishay-general-semiconductor-diodes-division/1N914TAP/1N914TAPGICT-ND/8564478 | 1N914TAPGICT-ND | 6,1N914TAPGICT-ND
D14 | 1 | SB230TA | SMC | SB230TA | Diode_THT:D_DO-41_SOD81_P7.62mm_Horizontal | https://www.digikey.com.au/product-detail/en/smc-diode-solutions/SB230TA/1655-1518-1-ND/6022963 | 1655-1518-1-ND | 1,1655-1518-1-ND
D15 | 1 | D_TVS | Littelfuse | TP6KE47A | Diode_THT:D_DO-15_P12.70mm_Horizontal |  | F6853CT-ND | 1,F6853CT-ND
D1 D2 D3 D4 D7 D8 D9 D10 | 8 | LED | Wurth | 151031SS04000 | LED_THT:LED_D3.0mm | https://www.digikey.com.au/product-detail/en/w%C3%BCrth-elektronik/151031SS04000/732-5005-ND/4489979 | 732-5005-ND | 8,732-5005-ND
F1 F2 | 2 | Polyfuse | Bel Fuse | 0ZRP0050FF1E | Fuse:Fuse_BelFuse_0ZRE0055FF_L14.0mm_W4.1mm | https://www.digikey.com.au/product-detail/en/bel-fuse-inc/0ZRP0050FF1E/507-2403-ND/9468252 | 507-2403-ND | 2,507-2403-ND
IC3 | 2 | Trig Cond Socket | Sullins Connector Solutions | PPTC041LFBN-RC | Package_DIP:DIP-8_W7.62mm_Socket |  | S7002-ND | 2,S7002-ND
J4 | 1 | Conn_02x20_Counter_Clockwise | Sullins | SBH11-PBPC-D20-ST-BK | Connector_IDC:IDC-Header_2x20_P2.54mm_Vertical | https://www.digikey.com.au/product-detail/en/sullins-connector-solutions/SBH11-PBPC-D20-ST-BK/S9175-ND/1990068 | S9175-ND | 1,S9175-ND
Q1 Q2 Q3 Q4 | 4 | N-Channel MOSFET | ST | STP62NS04Z | Package_TO_SOT_THT:TO-220-3_Horizontal_TabDown |  | 497-5896-5-ND | 4,497-5896-5-ND
Q5 Q6 | 2 | Q_NMOS_GDSD | Vishay | IRLD024PBF | Package_DIP:Vishay_HVM-DIP-3_W7.62mm | https://www.digikey.com.au/product-detail/en/vishay-siliconix/IRLD024PBF/IRLD024PBF-ND/812492 | IRLD024PBF-ND | 2,IRLD024PBF-ND
R1 R2 R3 R4 R13 R14 R15 R16 R19 R20 R28 R43 | 12 | 100k | Vishay | MBA02040C1003FCT00 | Resistor_THT:R_Axial_DIN0204_L3.6mm_D1.6mm_P5.08mm_Horizontal | https://www.digikey.com.au/product-detail/en/vishay-beyschlag-draloric-bc-components/MBA02040C1003FCT00/BC3240CT-ND/6138743 | BC3240CT-ND | 12,BC3240CT-ND
R9 R10 R11 R12 R23 R24 R25 R26 R33 | 9 | 2.4k | Vishay | MBA02040C2401FC100 | Resistor_THT:R_Axial_DIN0204_L3.6mm_D1.6mm_P5.08mm_Horizontal | https://www.digikey.com.au/product-detail/en/vishay-beyschlag-draloric-bc-components/MBA02040C2401FC100/BC3483CT-ND/7350913 | BC3483CT-ND | 9,BC3483CT-ND
R30 | 1 | 3.9k | Vishay | MBA02040C3901FCT00 | Resistor_THT:R_Axial_DIN0204_L3.6mm_D1.6mm_P5.08mm_Horizontal | https://www.digikey.com.au/product-detail/en/vishay-beyschlag-draloric-bc-components/MBA02040C3901FCT00/BC3272CT-ND/6138775 | BC3272CT-ND | 1,BC3272CT-ND
R31 R32 R34 R38 R39 R40 R55 R62 R63 | 9 | 470R | Vishay | MBA02040C4700FRP00 | Resistor_THT:R_Axial_DIN0204_L3.6mm_D1.6mm_P5.08mm_Horizontal | https://www.digikey.com.au/product-detail/en/vishay-beyschlag-draloric-bc-components/MBA02040C4700FRP00/BC3516CT-ND/7350946 | BC3516CT-ND | 9,BC3516CT-ND
R35 R36 | 2 | 2.49k | Vishay | MBA02040C2491FRP00 | Resistor_THT:R_Axial_DIN0204_L3.6mm_D1.6mm_P5.08mm_Horizontal | https://www.digikey.com.au/product-detail/en/vishay-beyschlag-draloric-bc-components/MBA02040C2491FRP00/BC2-49KXCT-ND/336807 | BC2.49KXCT-ND | 2,BC2.49KXCT-ND
R27 R45 | 2 | 10k | Vishay | MBA02040C1002FRP00 | Resistor_THT:R_Axial_DIN0204_L3.6mm_D1.6mm_P5.08mm_Horizontal | https://www.digikey.com.au/product-detail/en/vishay-beyschlag-draloric-bc-components/MBA02040C1002FRP00/BC10-0KXCT-ND/336866 | BC10.0KXCT-ND | 2,BC10.0KXCT-ND
R46 | 1 | 120R | Vishay | MBA02040C1200FC100 | Resistor_THT:R_Axial_DIN0204_L3.6mm_D1.6mm_P5.08mm_Horizontal |  | BC3453CT-ND | 1,BC3453CT-ND
R5 R6 R7 R8 R17 R18 R21 R22 R29 R37 R41 R42 R44 R47 R53 R54 | 16 | 1k | Vishay | MBA02040C1001FRP00 | Resistor_THT:R_Axial_DIN0204_L3.6mm_D1.6mm_P5.08mm_Horizontal |  | BC1.00KXCT-ND | 16,BC1.00KXCT-ND
R52 | 1 | 2k | Vishay | MBA02040C2001FCT00 | Resistor_THT:R_Axial_DIN0204_L3.6mm_D1.6mm_P5.08mm_Horizontal | https://www.digikey.com.au/product-detail/en/vishay-beyschlag-draloric-bc-components/MBA02040C2001FCT00/BC3254CT-ND/6138757 | BC3254CT-ND | 1,BC3254CT-ND
U1 U3 | 2 | SP721 | Littelfuse | SP721APP | Package_DIP:DIP-8_W7.62mm |  | F2720-ND | 2,F2720-ND
U2 U4 | 2 | TC4424A | Microchip | TC4424AVPA | Package_DIP:DIP-8_W7.62mm_Socket | https://www.digikey.com.au/product-detail/en/microchip-technology/TC4424AVPA/TC4424AVPA-ND/1098910 | TC4424AVPA-ND | 2,TC4424AVPA-ND
U5 | 1 | MPX4250 | NXP | MPX4250AP | Misc:MPX4250 | https://www.digikey.com.au/product-detail/en/nxp-usa-inc/MPX4250AP/MPX4250AP-ND/464053 | MPX4250AP-ND | 1,MPX4250AP-ND
U6 | 1 | ULN2003 | TI | ULN2003AIN‎ | Package_DIP:DIP-16_W7.62mm | https://www.digikey.com.au/product-detail/en/texas-instruments/ULN2003AIN/296-16971-5-ND/653041 | 296-16971-5-ND | 1,296-16971-5-ND
U8 | 1 | LM2940S-5.0 | ON Semi | NCV7805BTG | Package_TO_SOT_THT:TO-220-3_Horizontal_TabDown | https://www.digikey.com.au/product-detail/en/on-semiconductor/NCV7805BTG/NCV7805BTGOS-ND/921437 | NCV7805BTGOS-ND | 1,NCV7805BTGOS-ND

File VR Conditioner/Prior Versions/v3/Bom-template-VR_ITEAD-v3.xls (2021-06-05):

NOTES:
1, Manufacture Part Number is critical. Customers should provide the exact MPN.
2, Components Supplier: Digi-Key，Mouser，Element14，Chip One Stop，Verical，P&S，MCM，Newark，Gerber，Future，Avnet Arrow，Wpi，Master，Onlinecomponents.com，TTI，Garrett，4Stat，Allied，AIPCO，Sierra IC，Advanced MP Technology，Components Direct，Bristol，Bisco，Quest Components，Area51，Coilcraft
3, We only source components from the listed suppliers. If the components can not be sourced from the above suppliers, customers should find a replacement or ship the components to us.
4, We recommend to use Yageo resistors, we can get a better price for customers. Here's the part number:
http://www.digikey.com/product-search/en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
http://www.digikey.com/product-search/en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
Ref | Value | Footprint | Manufacture | Manufacture Part Number | Quantity | Specification | Pads/Pins
C1 | CAP CER 0.1UF 50V Y5V 0805 | 0805 | Yageo | CC0805ZRY5V9BB104 | 1 | https://www.digikey.com.au/product-detail/en/yageo/CC0805ZRY5V9BB104/311-1361-1-ND/2103145 | 2
C2 | CAP CER 10000PF 50V X7R 0805 | 0805 | Yageo | CC0805KRX7R9BB103 | 1 | https://www.digikey.com.au/product-detail/en/yageo/CC0805KRX7R9BB103/311-1136-1-ND/303046 | 2
C3 | CAP CER 1UF 16V X7R 0805 | 0805 | Yageo | CC0805KKX7R7BB105 | 1 | https://www.digikey.com.au/product-detail/en/yageo/CC0805KKX7R7BB105/311-1365-1-ND/2103149 | 2
C4,C5 | CAP CER 1000PF 50V X7R 0805 | 0805 | Yageo | CC0805KRX7R9BB102 | 2 | https://www.digikey.com.au/product-detail/en/yageo/CC0805KRX7R9BB102/311-1127-1-ND/303037 | 4
R7,R9,R11,R13 | RES SMD 10K OHM 5% 1/8W 0805 | 0805 | Yageo | RC0805JR-0710KL | 4 | https://www.digikey.com.au/product-detail/en/yageo/RC0805JR-0710KL/311-10KARCT-ND/731188 | 8
MAX9926 | IC SENSOR INTERFACE VARI 16-QSOP | 16-QSOP | Maxim | MAX9926UAEE+TCT-ND | 1 | https://www.digikey.com.au/product-detail/en/MAX9926UAEE+T/MAX9926UAEE+TCT-ND/3879279 | 16
R4,R6 | RES SMD 1K OHM 5% 1/8W 0805 | 0805 | Yageo | RC0805JR-071KL | 2 | https://www.digikey.com.au/product-detail/en/yageo/RC0805JR-071KL/311-1.0KARCT-ND/731165 | 4

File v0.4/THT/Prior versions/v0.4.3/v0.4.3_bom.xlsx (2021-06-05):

QTY Full | Board Reference Full | Value | Type | Information | Included | Manufacturer | Model# | Digikey P/N | Mouser P/N | Digikey Price (USD) | Mouser Price (USD) | CTM Full Digikey | CTM Full Mouser | CTM 2 Ch Digikey | CTM 2 Ch Mouser | Note | Full Digikey import | 2Ch Digikey import | General Description | Mouser Full
 |  |  |  |  |  |  |  |  |  |  |  |  |  |  |  |  |  |  | x
1 | C16 | 10uF | CAP TANT 10UF 35V 10% RADIAL | Tantalum |  | Kemet | T356G106K035AT | 399-3654-ND (http://www.digikey.com/product-detail/en/TAP106K035SCS/478-1842-ND/563945) | 80-T356G106K035AT | $1.70 | $1.70 | $1.70 | $1.70 | $1.70 | $1.70 |  | 1,399-3654-ND | 1,399-3654-ND | Capacitor - 1x 10uF | 80-T356G106K035AT|1 | T356G106K035AT 1
6 | C2,C4,C6,C8,C10,C24 | 0.22uF | CAP CER 0.22UF 50V 10% RADIAL | X7R |  | Kemet | K224K20X7RF5UH5 | BC2678CT-ND | 594-K224K20X7RF5UH5 | $0.66 | $0.66 | $3.96 | $3.96 | $3.96 | $3.96 |  | 6,BC2678CT-ND | 6,BC2678CT-ND | Capacitor - 6x 0.22uF | 594-K224K20X7RF5UH5|6 | K224K20X7RF5UH5 6
7 | C1,C3,C5,C7,C9,C13,C15 | 0.1uF / 100nF | CAP CER 0.1UF 50V 20% RADIAL | X7R |  | Vishay | K104K15X7RF53H5 | BC3323-ND | 80-C322C104M5R-TR | $0.36 | $0.32 | $2.52 | $2.24 | $2.52 | $2.24 |  | 7,BC3323-ND | 7,BC3323-ND | Capacitor - 7x 0.1uF / 100nF | 80-C322C104M5R-TR|7 | K104K15X7RF53H5 7
1 | C14 | 47uF | CAP TANT 47UF 6.3V 10% RADIAL | Tantalum |  | Kemet | T356F476K006AT | 399-3652-ND (http://search.digikey.com/us/en/products/TAP476K010SCS/478-1910-ND/564013) | 80-T356F476K6AT | $1.57 | $1.57 | $1.57 | $1.57 | $1.57 | $1.57 |  | 1,399-3652-ND | 1,399-3652-ND | Capacitor - 1x 47uF | 80-T356F476K6AT|1 | T356F476K006AT 1
1 | C18 | 0.33uF | CAP CER 0.33UF 50V 10% RADIAL | X7R |  | AVX Corporation | AR215F334K4R | 478-5120-ND (http://search.digikey.com/us/en/products/FK14X7R1H334K/445-5312-ND/2256792) | 581-AR215F334K4R | $0.62 | $0.43 | $0.62 | $0.43 | $0.62 | $0.43 |  | 1,478-5120-ND | 1,478-5120-ND | Capacitor - 1x 0.33uF | 581-AR215F334K4R|1 | AR215F334K4R 1
2 | C19,C25 | 0.01uF | CAP CER 10000PF 50V 10% RADIAL | X7R |  | Kemet | C317C103K5R5TA | 399-4206-ND (http://www.digikey.com/product-detail/en/C315C103K5R5TA/399-4148-ND/817924) | 80-C317C103K5R | $0.24 | $0.24 | $0.48 | $0.48 | $0.48 | $0.48 |  | 2,399-4206-ND | 2,399-4206-ND | Capacitor - 2x 0.01uF | 80-C317C103K5R|2 | C317C103K5R5TA 2
3 | C11,C12,C20 | 1uF | CAP CER 1UF 50V 20% RADIAL | X7R |  | Kemet | C330C105M5U5TA | 399-4390-ND | 80-C330C105M5U | $0.66 | $0.66 | $1.98 | $1.98 | $1.32 | $1.32 |  | 3,399-4390-ND | 2,399-4390-ND | Capacitor - 3x 1uF | 80-C330C105M5U|3 | C330C105M5U5TA 3
1 | C23 | 4.7nF | CAP CER 4700PF 100V 10% RADIAL | X7R |  | Kemet | C317C472K1R5TA | 399-4243-ND | 80-C317C472K1R | $0.25 | $0.25 | $0.25 | $0.25 | $0.25 | $0.25 |  | 1,399-4243-ND | 1,399-4243-ND | Capacitor - 1x 4.7nF | 80-C317C472K1R|1 | C317C472K1R5TA 1
1 | D16 | 1N5919BG Zener | DIODE ZENER 5.6V 3W AXIAL | DO-41 |  | ON Semiconductor | 1N5919BG | 1N5919BGOS-ND | 863-1N5919BRLG | $0.34 | $0.43 | $0.34 | $0.43 | $0.34 | $0.43 |  | 1,1N5919BGOS-ND | 1,1N5919BGOS-ND | Diode - 1x 1N5919BG Zener | 863-1N5919BRLG|1 | 1N5919BG 1
2 | D15,D17 | 1N5818-TP Schottky | DIODE SCHOTTKY 1A 30V DO41 | DO-41 |  | Micro Commercial Co | 1N5818-TP | 1N5818-TPCT-ND (http://search.digikey.com/us/en/products/1N5818-TP/1N5818-TPCT-ND/950587) | 833-1N5818-TP | $0.39 | $0.39 | $0.78 | $0.78 | $0.78 | $0.78 |  | 2,1N5818-TPCT-ND | 2,1N5818-TPCT-ND | Diode - 2x 1N5818-TP Schottky | 833-1N5818-TP|2 | 1N5818-TP 2
8 | LED1,LED2,LED3,LED4,LED5,LED6,LED7,LED8 | LED-Red | LED SS 3MM 625NM RED DIFF | 5mm-LED |  |  | LTL-4221N | 160-1139-ND | 859-LTL-4221N | $0.47 | $0.10 | $3.76 | $0.80 | $1.88 | $0.40 |  | 8,160-1139-ND | 4,160-1139-ND | Diode - 8x LED-Red | 859-LTL-4221N|8 | LTL-4221N 8
4 | D9,D10,D11,D12 | 1N4004 | DIODE GEN PURPOSE 400V 1A DO41 | DO-41 |  | Micro Commercial Co | 1N4004-TP | 1N4004-TPMSCT-ND | 833-1N4004-TP | $0.11 | $0.11 | $0.44 | $0.44 | $0.22 | $0.22 |  | 4,1N4004-TPMSCT-ND | 2,1N4004-TPMSCT-ND | Diode - 4x 1N4004 | 833-1N4004-TP|4 | 1N4004-TP 4
 |  |  |  |  |  |  |  |  |  |  |  |  |  |  |  |  |  |  | x
1 | U2 | Surge Protection | VARISTOR 22V 3KA DISC 14MM | Disc 14mm |  | Bournes Inc | V14E14AUTO | F6389-ND |  | $0.72 | $0.72 | $0.72 | $0.72 | $0.72 | $0.72 |  | 1,F6389-ND | 1,F6389-ND | 1x Surge Protection |  | V14E14AUTO 1
 |  |  |  |  |  |  |  |  |  |  |  |  |  | $0.00 | $0.00 |  |  |  | x
1 | J3 | Dual Terminal Block | TERMINAL BLOCK 5MM VERT 2POS PCB |  |  | On Shore Technology Inc | OSTTA020161 | ED2561-ND | 571-2828362 | 0.402 | 0.51 | $0.40 | $0.51 | $0.40 | $0.51 | Quite expensive from digikey, cheaper elsewhere | 1,ED2561-ND | 1,ED2561-ND | 1x Dual Terminal Block | 571-2828362|1 | OSTTA020161 1
5 | Jumpers for male pins | Jumper | SHUNT JUMPER .1" BLACK GOLD |  |  |  | 969102-0000-DA | 3M9580-ND | 517-9691020000DA | $0.10 | $0.10 | $0.50 | $0.50 | $0.50 | $0.50 |  | 5,3M9580-ND | 5,3M9580-ND | 5x Jumper | 517-9691020000DA|5 | 969102-0000-DA 5
4 | Male pins | 40 POS 0.100 Pin Header | CONN HEADER .100" SNGL STR 40POS |  |  | Sullins Connector Solutions | PREC040SAAN-RC.. | S1012EC-40-ND | 571-41037410 | $0.56 | $2.95 | $2.24 | $11.80 | $2.24 | $11.80 | Mouser price is crazy | 4,S1012EC-40-ND | 4,S1012EC-40-ND | 4x 40 POS 0.100 Pin Header | 571-41037410|4 | PREC040SAAN-RC.. 4
1 | J4 | Rectangular Connectors - Headers, Male Pins | IDC BOX HEADER .100" 40POS |  |  | CNC Tech | 3020-40-0100-00 | 1175-1614-ND | 571-5103308-8 | $1.13 | $2.00 | $1.13 | $2.00 | $1.13 | $2.00 |  | 1,1175-1614-ND | 1,1175-1614-ND | 1x Rectangular Connectors - Headers, Male Pins | 571-5103308-8|1 | 3020-40-0100-00 1
 |  |  |  |  |  |  |  |  |  |  |  |  |  |  |  |  |  |  | x
8 | Q1,Q2,Q3,Q4,Q5,Q6,Q7,Q8 | 62A MOSFET N-CH | MOSFET N-CH 33V TO-220 | TO-220 |  | STMicroelectronics | STP75NS04Z | 497-5981-5-ND | 511-STP62NS04Z | $1.51 | $1.51 | $12.08 | $12.08 | $9.06 | $9.06 |  | 8,497-5981-5-ND | 6,497-5981-5-ND | 8x 62A MOSFET N-CH | 511-STP62NS04Z|8 | STP75NS04Z 8
1 | R54 | 10k | RES 10.0K OHM 1/4W 1% METAL FILM |  |  | Yageo | MFR-25FBF52-10K | 10.0KXBK-ND (http://search.digikey.com/us/en/products/MFR-25FBF-10K0/10.0KXBK-ND/13219) | 71-RN60D-F-10K | $0.08 | $0.11 | $0.08 | $0.11 | $0.08 | $0.11 |  | 1,10.0KXBK-ND | 1,10.0KXBK-ND | Resistor - 1x 10k | 71-RN60D-F-10K|1 | MFR-25FBF52-10K 1
17 | R10,R13,R16,R19,R21,R23,R24,R29,R30,R39,R40,R50,R51,R57,R58,R59,R60 | 1k | RES 1.00K OHM 1/4W 1% METAL FILM |  |  | Yageo | MFR-25FBF52-1K | 1.00KXBK-ND | 71-RN60D-F-1.0K | $0.06 | $0.11 | $1.02 | $1.87 | $0.78 | $1.43 |  | 17,1.00KXBK-ND | 13,1.00KXBK-ND | Resistor - 17x 1k | 71-RN60D-F-1.0K|17 | MFR-25FBF52-1K 17
4 | R9,R12,R15,R18 | 680 | RES 680 OHM 0.6W 1% AXIAL |  |  | TE Connectivity | 1622545-1 | A105963CT-ND | 279-LR1F680R | $0.22 | $0.15 | $0.88 | $0.60 | $0.44 | $0.30 | LED current limiting resistors | 4,A105963CT-ND | 2,A105963CT-ND | Resistor - 4x 680 | 279-LR1F680R|4 | 1622545-1 4
6 | R2,R4,R6,R8,R22,R41 | 470 | RES METAL FILM 1/4W 470 OHM 1% AXIAL |  |  | Stackpole Electronics Inc | RNF14FTD470R | RNF14FTD470RCT-ND | 279-LR1F470R | $0.11 | $0.15 | $0.66 | $0.90 | $0.66 | $0.90 |  | 6,RNF14FTD470RCT-ND | 6,RNF14FTD470RCT-ND | Resistor - 6x 470 | 279-LR1F470R|6 | RNF14FTD470R 6
7 | R1,R3,R26,R28,R33,R34,R61 | 1% 2.49k | 2.49k Ohm ±1% 0.25W, 1/4W Through Hole Resistor Axial Metal Film | For GM Sensors |  | Yageo | MFR-25FBF52-2K49 | 2.49KXBK-ND (http://search.digikey.com/us/en/products/RC55Y-2K49BI/985-1047-1-ND/2401912) | 603-MFR-25FBF52-2K49 | $0.14 | $0.16 | $0.98 | $1.12 | $0.70 | $0.80 |  | 7,2.49KXBK-ND | 5,2.49KXBK-ND | Resistor - 7x 1% 2.49k | 603-MFR-25FBF52-2K49|7 | MFR-25FBF52-2K49 7
1 | R7 | 0.1% 3.9k | RES 3.9K OHM 1/4W 0.1% METAL FILM AXL |  |  | Yageo | MFP-25BRD52-3K9 | 3.9KADCT-ND (http://search.digikey.com/us/en/products/MFP-25BRD52-3K9/3.9KADCT-ND/2059137) | 279-H83K9BDA | $0.46 | $1.10 | $0.46 | $1.10 | $0.46 | $1.10 | Battery reference (Voltage divider) | 1,3.9KADCT-ND | 1,3.9KADCT-ND | Resistor - 1x 0.1% 3.9k | 279-H83K9BDA|1 | MFP-25BRD52-3K9 1
12 | R11,R14,R17,R20,R35,R36,R37,R38,R48,R49,R55,R56 | 100k | RES 100K OHM 1/4W 1% METAL FILM |  |  | Yageo | MFR-25FBF52-100K | 100KXBK-ND (http://search.digikey.com/us/en/products/MFR-25FBF-100K/100KXBK-ND/13473) | 603-FMF-25FTF52100K | $0.10 | $0.10 | $1.20 | $1.20 | $0.80 | $0.80 |  | 12,100KXBK-ND | 8,100KXBK-ND | Resistor - 12x 100k | 603-FMF-25FTF52100K|12 | MFR-25FBF52-100K 12
4 | R25,R27,R31,R32 | 160 | RES 10 OHM 2W 5% AXIAL |  |  | Yageo | FMP200JR-52-10R | 10ZCT-ND |  | $0.27 | $0.23 | $1.08 | $0.92 | $0.54 | $0.46 |  | 4,10ZCT-ND | 2,10ZCT-ND | Resistor - 4x 160 |  | FMP200JR-52-10R 4
1 | U1 | LM2940T-5.0/NOPB | IC REGULATOR LDO LM2940-5.0 1A TO220 | TO-220 |  | Texas Instruments | LM2940T-5.0/NOPB | LM2940T-5.0/NOPB | 926-LM2940T-5.0/NOPB | $1.68 | $1.67 | $1.68 | $1.67 | $1.68 | $1.67 |  | 1,LM2940T-5.0/NOPB | 1,LM2940T-5.0/NOPB | 1x LM2940T-5.0/NOPB | 926-LM2940T-5.0/NOPB|1 | LM2940T-5.0/NOPB 1
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

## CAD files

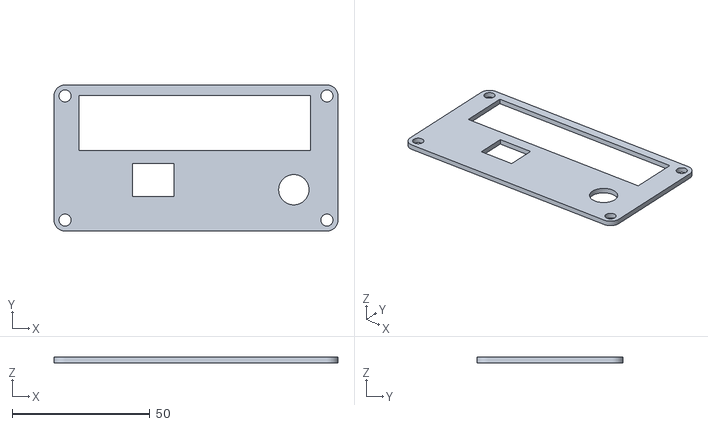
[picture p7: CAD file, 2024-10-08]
PNPs/Miata NA6/Latest/Case/MX5-PNP-Endplate.stl
103.0 x 53.0 x 2.00

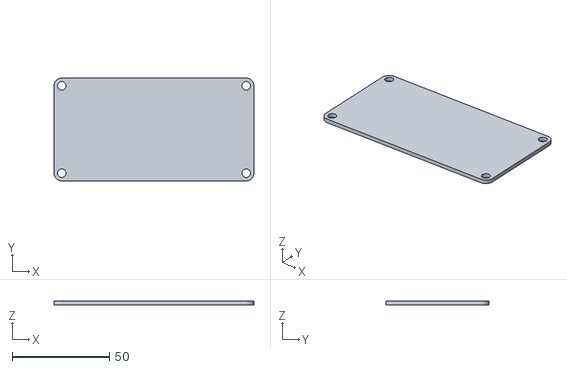
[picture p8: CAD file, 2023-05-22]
PNPs/Miata NA6/Latest/Case/MX5-PNP-Backplate.stl
103.0 x 53.0 x 2.00

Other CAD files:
PNPs/Miata NA6/Latest/Case/MX5-PNP-Backplate.dxf
PNPs/Miata NA6/Latest/Case/MX5-PNP-Endplate.dxf

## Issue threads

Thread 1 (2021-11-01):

0.4.3d 22uf ceramic capacitor in reset protection

oleh-danilovskyi, 2021-11-01:
I can see that 0.4.3d has C19 22uf  in "Reset protection". It is
FA22X7R1E226MRU06 and pretty expensive. According to AVR040 4.7nf should be used for reset pin protection . Actually previous version of speeduino  used 4.7nf instead of 22uf. Is there a need to have there such "big" capacitor?

turboedge, 2021-11-01:
If you really want it to prevent any resets, even ones caused by connecting the USB cable and other things, then the higher value is required. The lower values are just to prevent interference from causing a reset. There are other 22uf ceramic capacitors that might be cheaper, and probably more than fine.

noisymime, 2024-02-05:
Short answer, yes, the bigger cap is needed with the 2560. For some reason it is very sensitive to the capacitor value (Much more so than other AVR MCUs).

As mentioned, other caps of similar values can certainly be used

Closed 2024-02-05.

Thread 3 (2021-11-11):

0.4.3d MAP sensor mounting hole blocked by Arduino USB connector

DeionSi, 2021-11-11:
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

tydelane, 2025-01-06:
Hi, did you find a solution to this? I am dealing with this issue right now

tydelane, 2025-01-07:
Well thank you for letting me know, I'm just finishing up assembling my
0.4.3d and I'm going to install it with a k24A4 in my 98 civic! I had to
get a replacement for the MAP sensor though since the recommended was
obsolete. I chose the MPX5700. Was the 4250 available when you built yours
or did you have to get a replacement as well?

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

kendoman96, 2025-01-07:
I didn't have to get a replacement. 2 years later turbo drift miata has issues with everything except the ECU lol

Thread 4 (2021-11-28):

0.4.3d (and others?) Hardware SPI pins used by non SPI

DeionSi, 2021-11-28:
It was noted that atmega2560 hardware SPI (PB0-3) pins (arduino mega D50-D53) are used by non SPI functions (clutch input, ignition 3 output, ignition 4 output). Perhaps these circuits could be moved to other outputs to not restrict SPI usage.

noisymime, 2021-11-28:
What's the actual use case here as there's no SPI support for things with these boards?

The v0.3/0.v4 can't and won't be changed on these pins. Any change here would need to be a whole new board.

DeionSi, 2021-11-30:
Actual possible use case would be for SD-card logging with something like https://electropeak.com/micro-sd-tf-card-adapter-module.
Even if not possible 0.3 or 0.4, this issue could be kept open as a reminder for future revisions. It is your choice.

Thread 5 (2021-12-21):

Issues or not ? On schematic v0.4.3.png

AmesisProject, 2021-12-21:
hello, there is not an error on the pins named between the ic igni 1 & 2 has the pins of the arduino on the board 0.43 ?
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

https://github.com/speeduino/Hardware/blob/main/v0.4/THT/Prior%20versions/v0.4.3/schematic%20v0.4.3_schem.png

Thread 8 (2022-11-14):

Resistors 25 27 31 32

AmesisProject, 2022-11-14:
Hello, I just noticed that a resistor is missing on the kicad version before the ignition output on the 0.4.3d file
While this resistance is on all the other files as well on the 0.3x 0.4x fritzing as the kicad CMS.
Is this normal? I can fix it and do a pullrequest on GitHub if you want it

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

turboedge, 2022-11-14:
Josh did some testing actually, and decided that those resistors were not required. So they were not included in newer versions.

noisymime, 2022-11-14:
Per comments on Facebook, those resistors are not required.

Closed 2022-11-14.

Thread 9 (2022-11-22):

Hardware versions schematics & PCB images

PSIG-dev, 2022-11-22:
Please ensure each hardware version has viewable/printable schematics and PCB images for user reference, troubleshooting, modifications and wiring, without requiring a special program to view.  Thanks!

PSIG-dev, 2023-02-15:
• Bump •

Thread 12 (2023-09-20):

v0.4.4.d BoM update needed

aceberns, 2023-09-20:
Hello guys,

Some parts in the v0.4.4.d BoM are obsolete and we need an update:

C6 C12 C13 C14 C7 C5 = Samsung | CL21B224KOCNNNC | 0.22uF SMD Capacitor - https://www.digikey.com/product-detail/en/samsung-electro-mechanics-america-inc/CL21B224KOCNNNC/1276-1284-1-ND/3889370

D4 D3 D8 D7 D1 D2 D9 D10 = Osram | LH R974-LP-1 | SMD LED - https://www.digikey.com/product-detail/en/osram-opto-semiconductors-inc/LH-R974-LP-1/475-1415-1-ND/1802604

F1 F2 = Bel Fuse | 0ZCC0050FF2C | SMD polyfuse - https://www.digikey.com.au/product-detail/en/bel-fuse-inc/0ZCC0050FF2C/507-1361-1-ND/1560228

U1 U3 U7 U9 = STMicro | VNLD5090-E | PWR DRIVER - https://www.digikey.com.au/products/en?keywords=VNLD5090-E

Could you please update, or inform a direct substitute? Thanks in advance!

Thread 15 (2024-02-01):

Gerber outline (gml/gko/gbr) file mising

bilbolodz, 2024-02-01:
In project gerber Board Outline (gml/gko/gbr) file is missing. Could you please provide these?

turboedge, 2024-02-01:
Which board is it missing for?

bilbolodz, 2024-02-01:
I've tried to put your gerber for VR Conditioner on DirtyPCBs and it complains about missing Board Outline
I also tried with:

- THT v0_4_3d
- SMD v0_4_4d
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

turboedge, 2024-02-01:
Dirty PCB is not detecting it properly. It is the file edge cuts or contour, depending on which board you are working with. That VR conditioner was uploaded by someone else, and does seem to be missing the outside edge. I would use the v3.1 instead.

bilbolodz, 2024-02-01:
VR v3.1 has problem too. Do you have contact to person responsible for VR conditioner board?

bilbolodz, 2024-02-01:
It's probably: https://github.com/TechColab/VR-Conditioner-MAX9926-reg

turboedge, 2024-02-01:
Just uploaded this to another supplier and it worked perfectly.

[(https://github.com/speeduino/Hardware/blob/5883efc2f211134b859203c3047a4003eb73300a/VR%20Conditioner/Prior%20Versions/v3/gerbers/VR%20Conditioner-v0.3.1.zip)]

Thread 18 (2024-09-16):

Na6 PNP V1.3 Bom D13, D14 Missing from excel file

rudutoitnuhome, 2024-09-16:
I've added D13 and D14 Zener Diode 5.6 V 3 W ±5% Through Hole Axial on the Bom

[Speeduino PNP NA 8995 v1.3 BOM.xlsx](https://github.com/user-attachments/files/17009789/Speeduino.PNP.NA.8995.v1.3.BOM.xlsx)

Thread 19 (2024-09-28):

Power Supply Component Mismatch: Suggested Replacements

OpenLogicEFI, 2024-09-28:
Noticed a few components need to be balanced in the power supply. I found some component that could serve as BOM drop in replacements.

**D15 has a max Vbr of 49.1v. Too high for D14 (30v) and U8 (35v).**
-Could swap D15 to SMBJ20A-Q. Vbr is 24.5v.

**C21 doesn't meet the ESR requirements of U8 ([page 15 - 8.1](https://www.ti.com/lit/ds/symlink/lm2940-n.pdf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)), which calls for a 'critical' use of 100mΩ - 1Ω ESR.**

-Could replace U8 to make it less strict (TLF80511TC / TLE42744GV50ATMA, 400mA max, Automotive) or (LM7805SX/NOPB / LM340S-5.0/NOPB, higher output, easier to get, reliable).

-Or, replace C21 with something like TPSB476K010R0250 (250mΩ) or TPSB476K010R0350 (350mΩ).

noisymime, 2024-09-28:
Not sure if I'm looking at a different data sheet or BOM, but the ESR I'm seeing of C21 (EEU-FC1H470B) is 600mΩ, which is very much in spec?

OpenLogicEFI, 2024-09-28:
I think you're looking the 0.4.3d THT BOM. I was looking at the 0.4.4d SMD board.

0.4.4d (https://github.com/speeduino/Hardware/blob/main/v0.4/SMD/Latest/v0.4.4d%20BOM.csv)

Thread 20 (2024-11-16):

Missing v0.4 SMD symbols after importing in KiCAD 8

Thrathra, 2024-11-16:
Hi, I'm currently working on the v0.4.4d SMD project.

It seems that some symbols are lacking after importing the project.
For instance, a diode is missing at the right of the power regulator page 4, and the circuit at the right of the S1 component is missing aswell on the same page.
Do I have to install additional libraries and if so, which ones?
Furthermore, it is not clear if I have to use the "v0.4.4d.kicad_pro" file or the "v0.4.4d.pro" as they have different sizes.

Thanks in advance!

turboedge, 2024-11-21:
I'd have to check that, but I can say that you should be using the .kicad_pro file. It will be the newer of the two. The .pro files were used with even older versions of the software, and Kicad does not remove them when the project is upgraded.

Thrathra, 2024-12-02:
Thanks for your response and sorry for the delay.
Here's a screenshot about the issue.
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
Do you have the same schematic or is an issue on my side?

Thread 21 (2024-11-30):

Unable to view A17 and A18 in TunerStudio for DropBear

Rozakiin, 2024-11-30:
In dropbear v2 ecu the spare Analog outputs are A17 and A18 but in TunerStudio the dropdown only goes to A16.

Not sure if this is a software issue or label issue of the PCB?

Rozakiin, 2024-12-01:
Upon further investigation this is due to the Speeduino ini file not listing the pins available for teensy. Therefore not relevant to the hardware.

https://github.com/speeduino/speeduino/issues/1191

This issue relates to the problem.

noisymime, 2024-12-01:
There are quite a few changes coming in the next release that will be adding support for a few things on Dropbear v2, this will be one of them.

Expecting this release out before Christmas.

Closed 2024-12-01.

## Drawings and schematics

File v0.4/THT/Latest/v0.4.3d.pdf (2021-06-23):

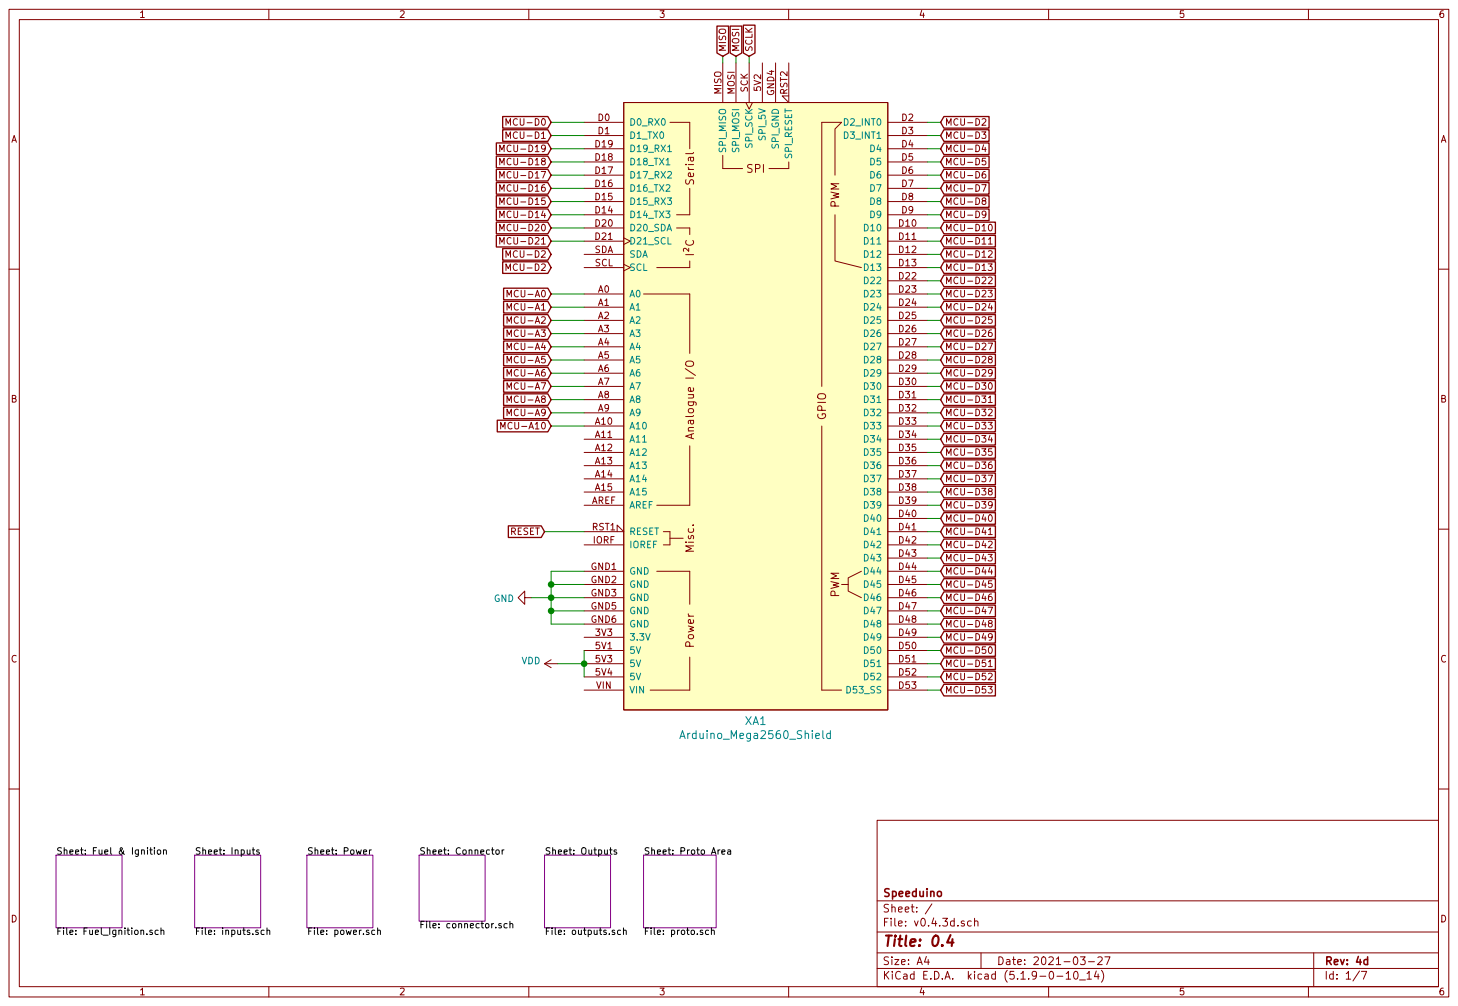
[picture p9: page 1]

File: outputs.sch GND

Sheet: Proto Area File: proto.sch

File: v0.4.3d.sch Sheet: / Speeduino

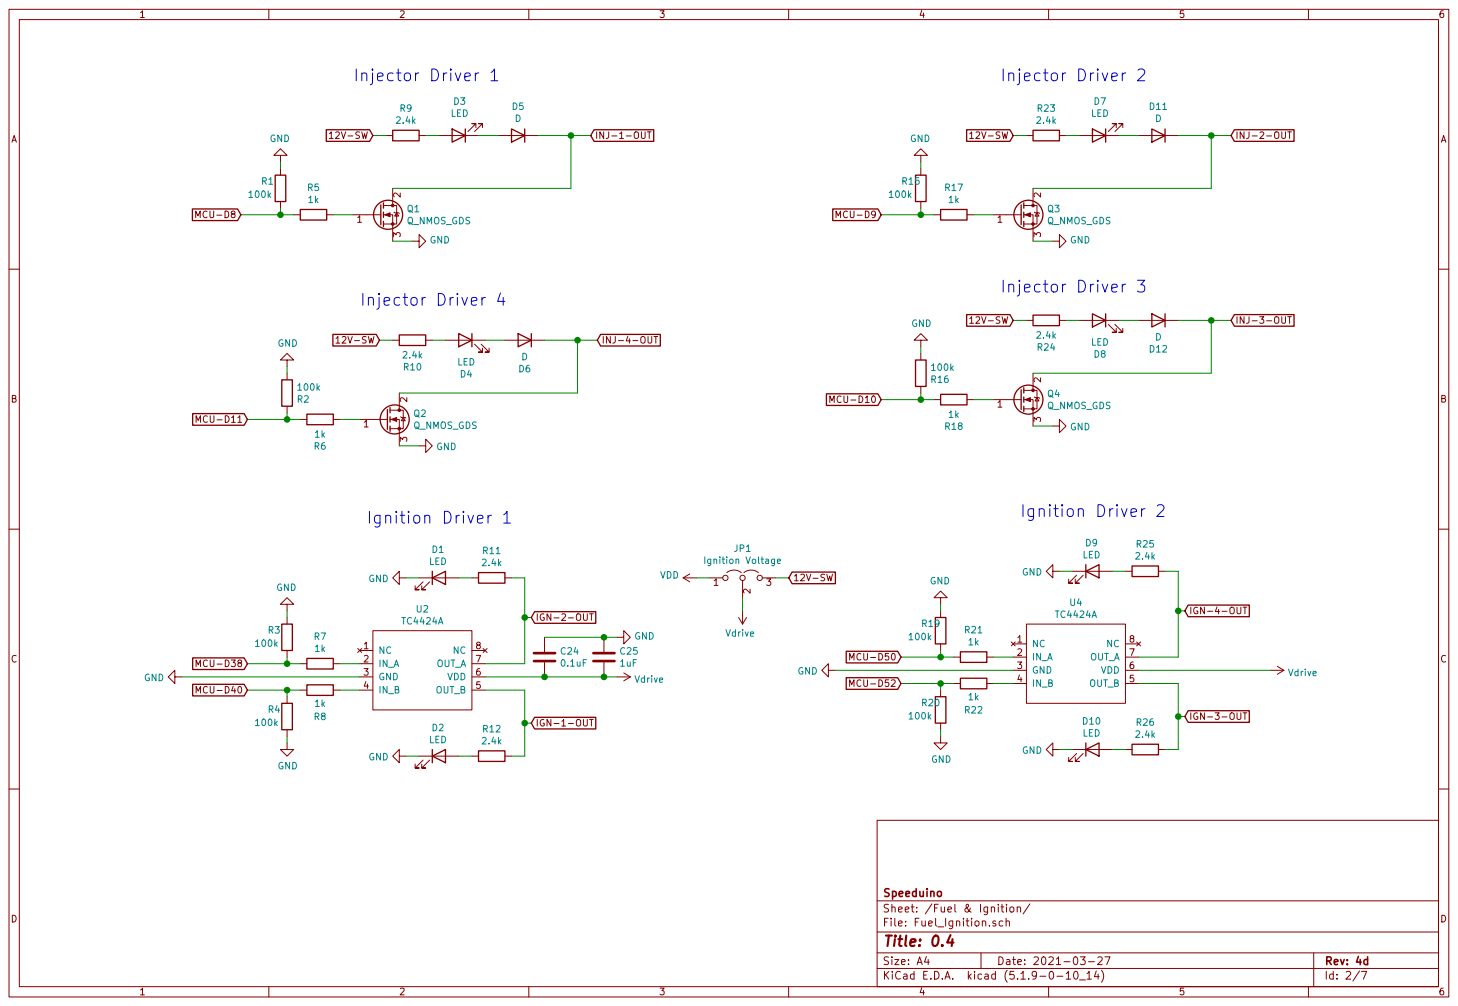
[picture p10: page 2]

Ignition Driver 2 Ignition Driver 1

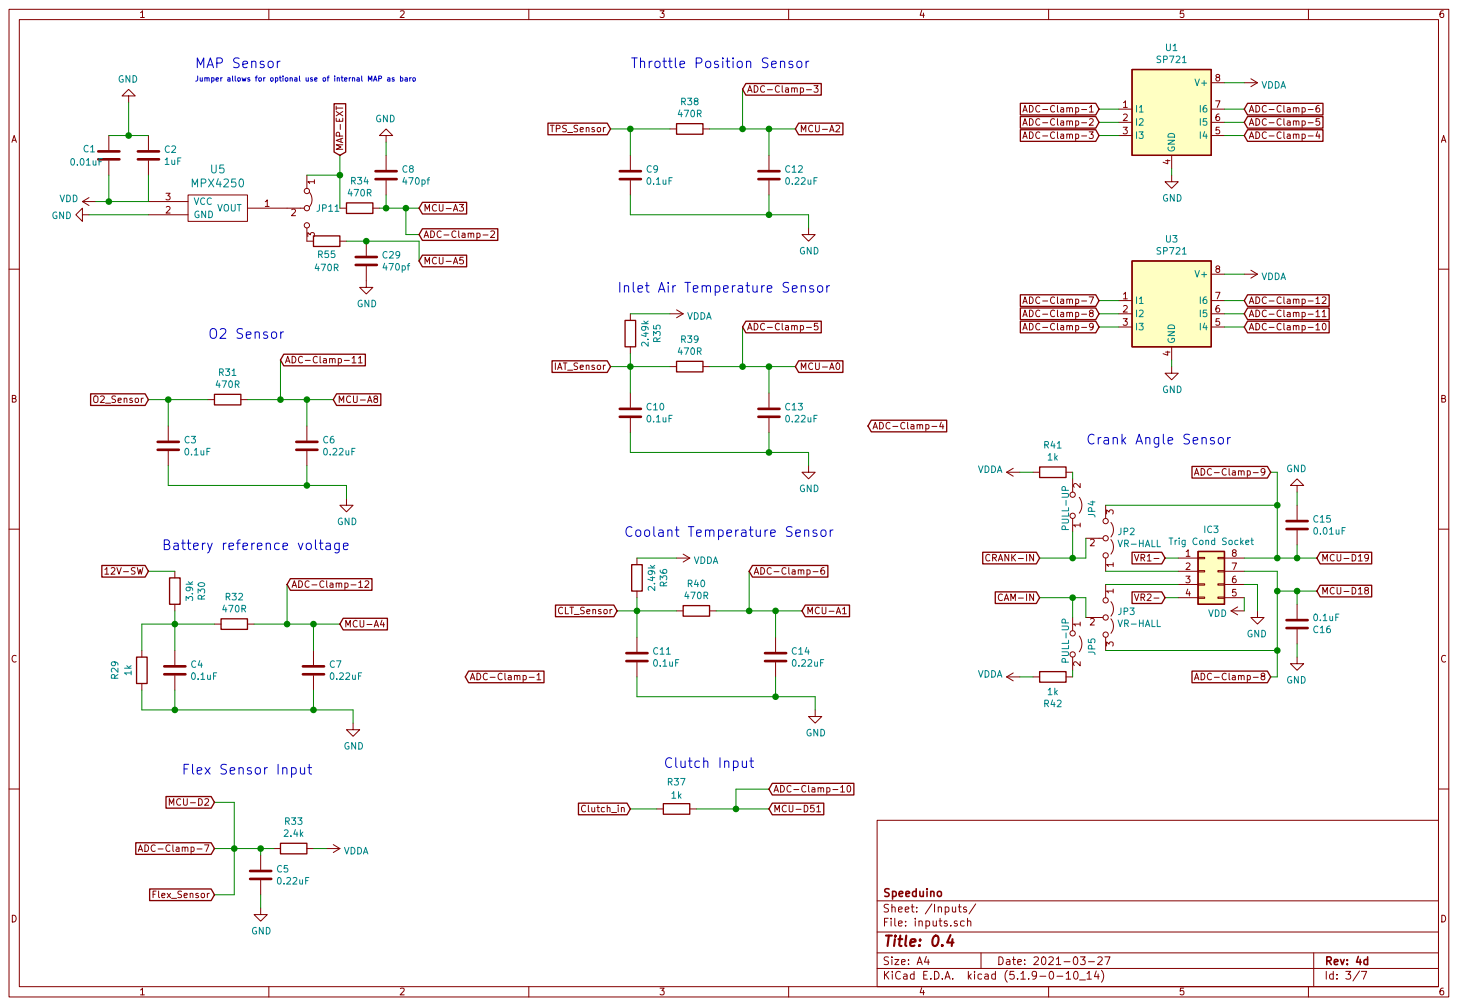
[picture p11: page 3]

Jumper allows for optional use of internal MAP as baro O2 Sensor

Inlet Air Temperature Sensor

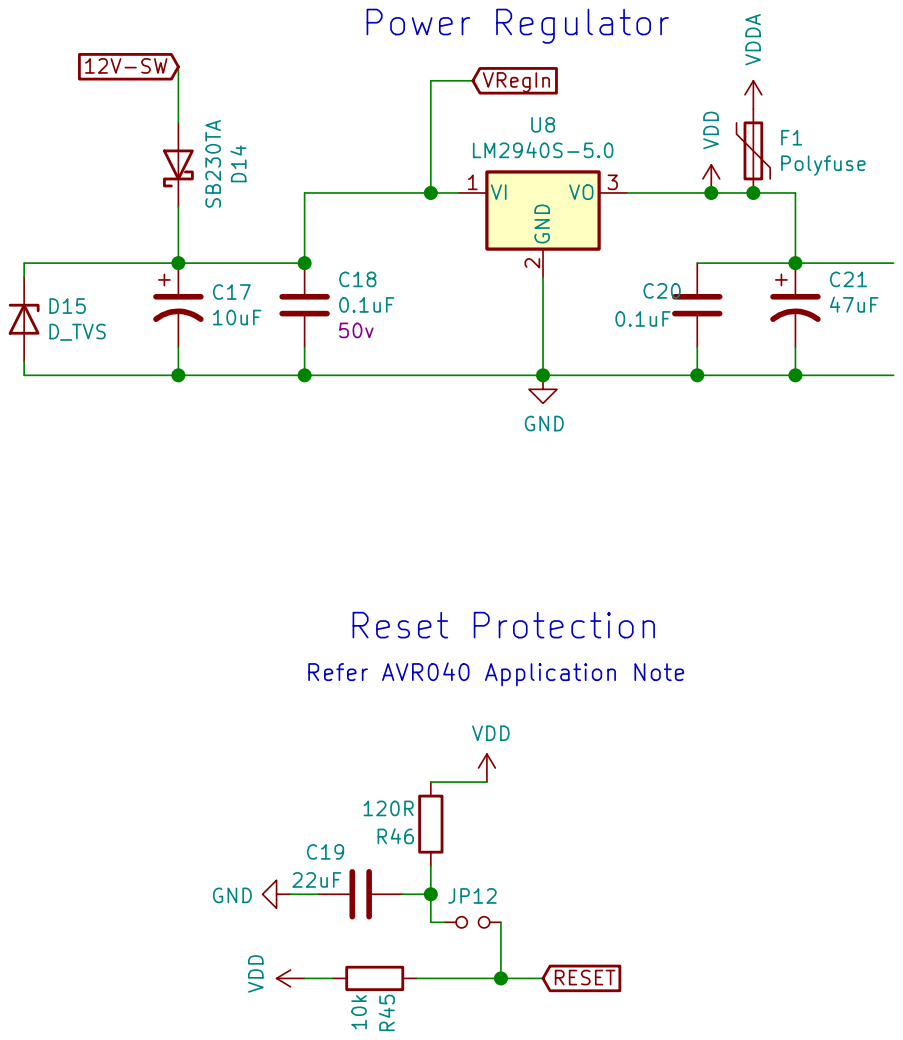
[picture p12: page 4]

File: power.sch Sheet: /Power/ Speeduino

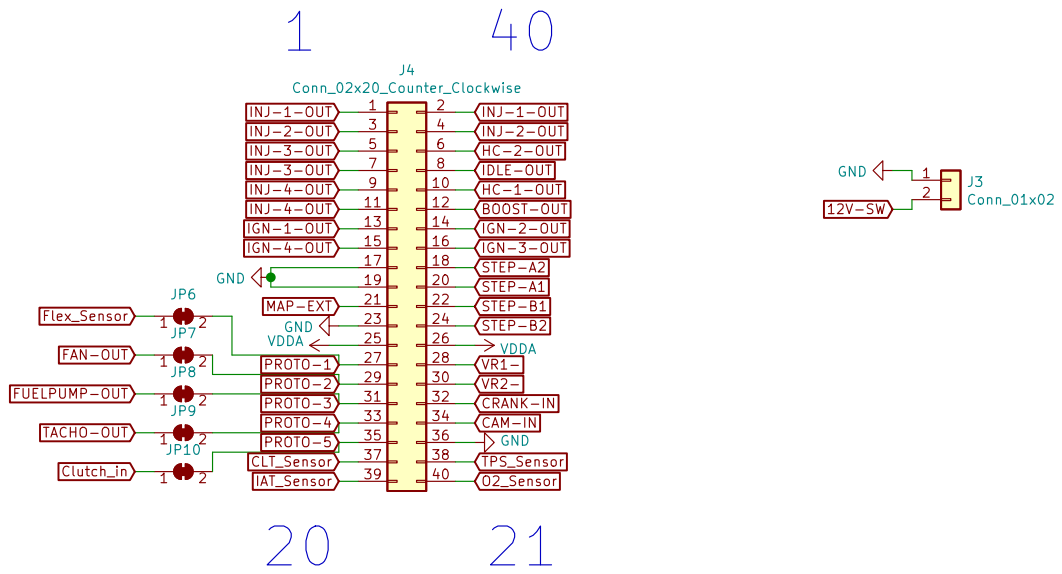
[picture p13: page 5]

IDLE-OUT PROTO-1 PROTO-2 PROTO-3 PROTO-4 PROTO-5
INJ-4-OUT

File: connector.sch Sheet: /Connector/ Speeduino GND

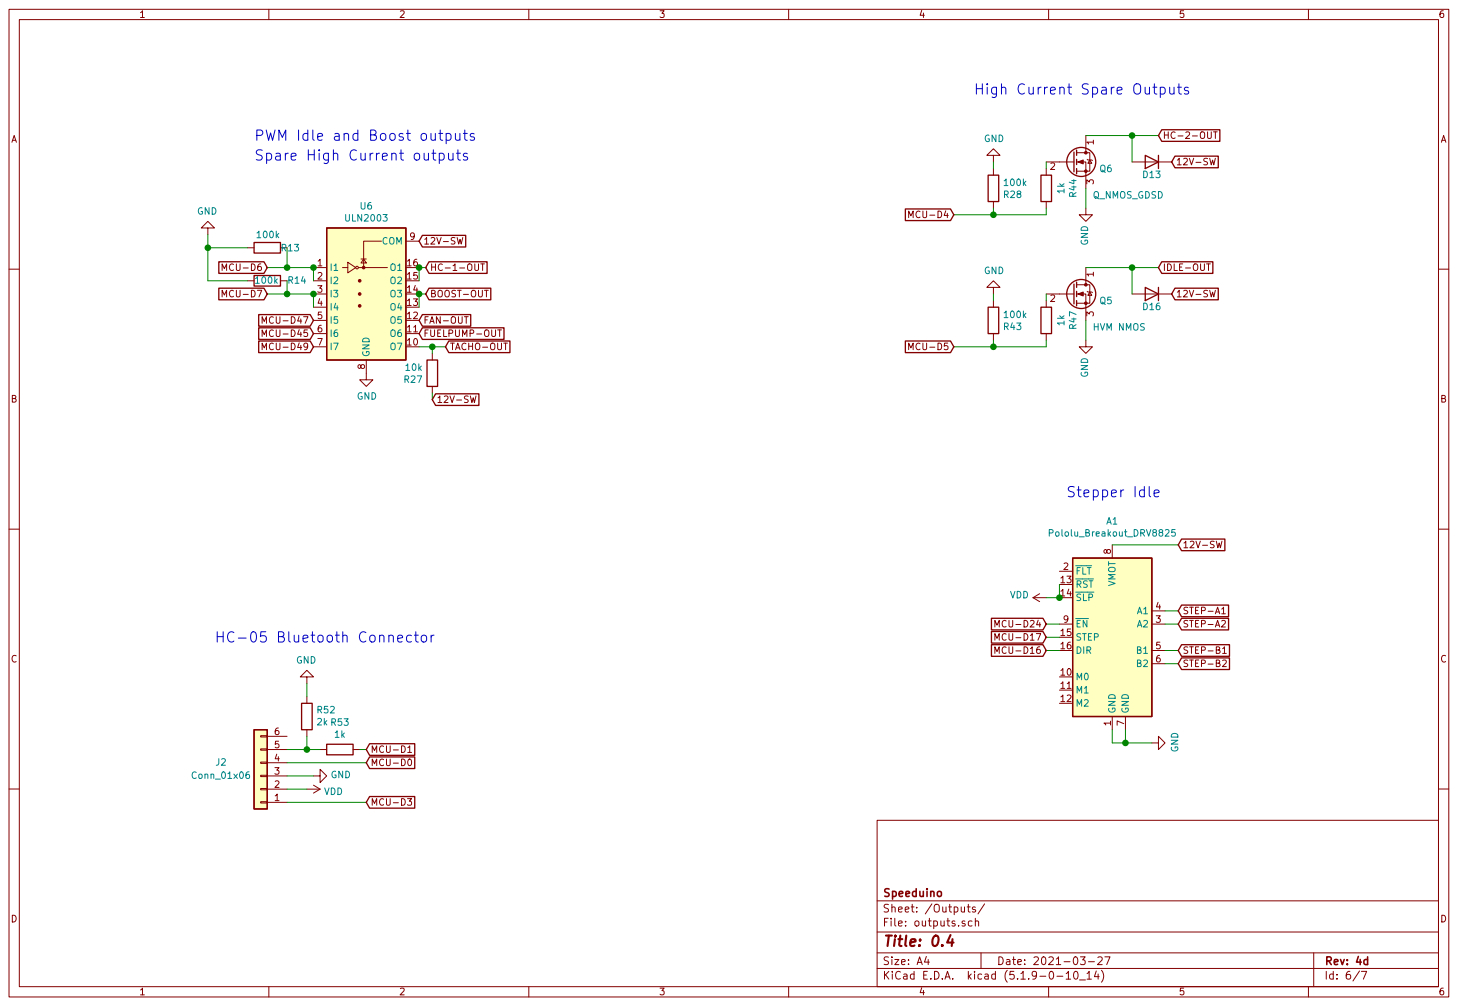
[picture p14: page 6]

High Current Spare Outputs

PWM Idle and Boost outputs

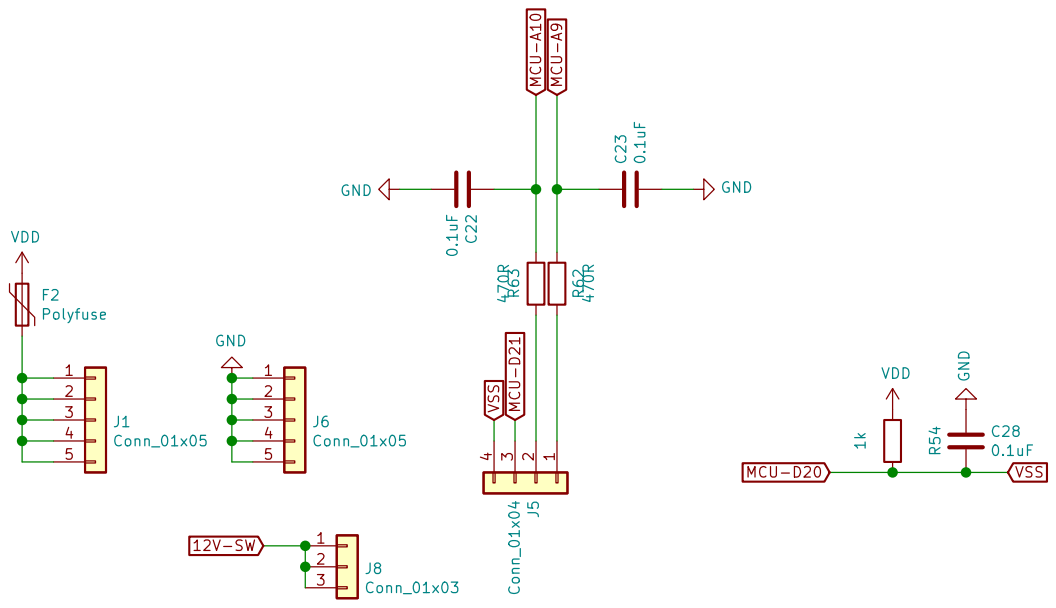
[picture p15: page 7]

1 J5 Conn_01x04 12V-SW MCU-A10 MCU-A9 VSS MCU-D20 VSS MCU-D21

File: proto.sch Sheet: /Proto Area/ Speeduino

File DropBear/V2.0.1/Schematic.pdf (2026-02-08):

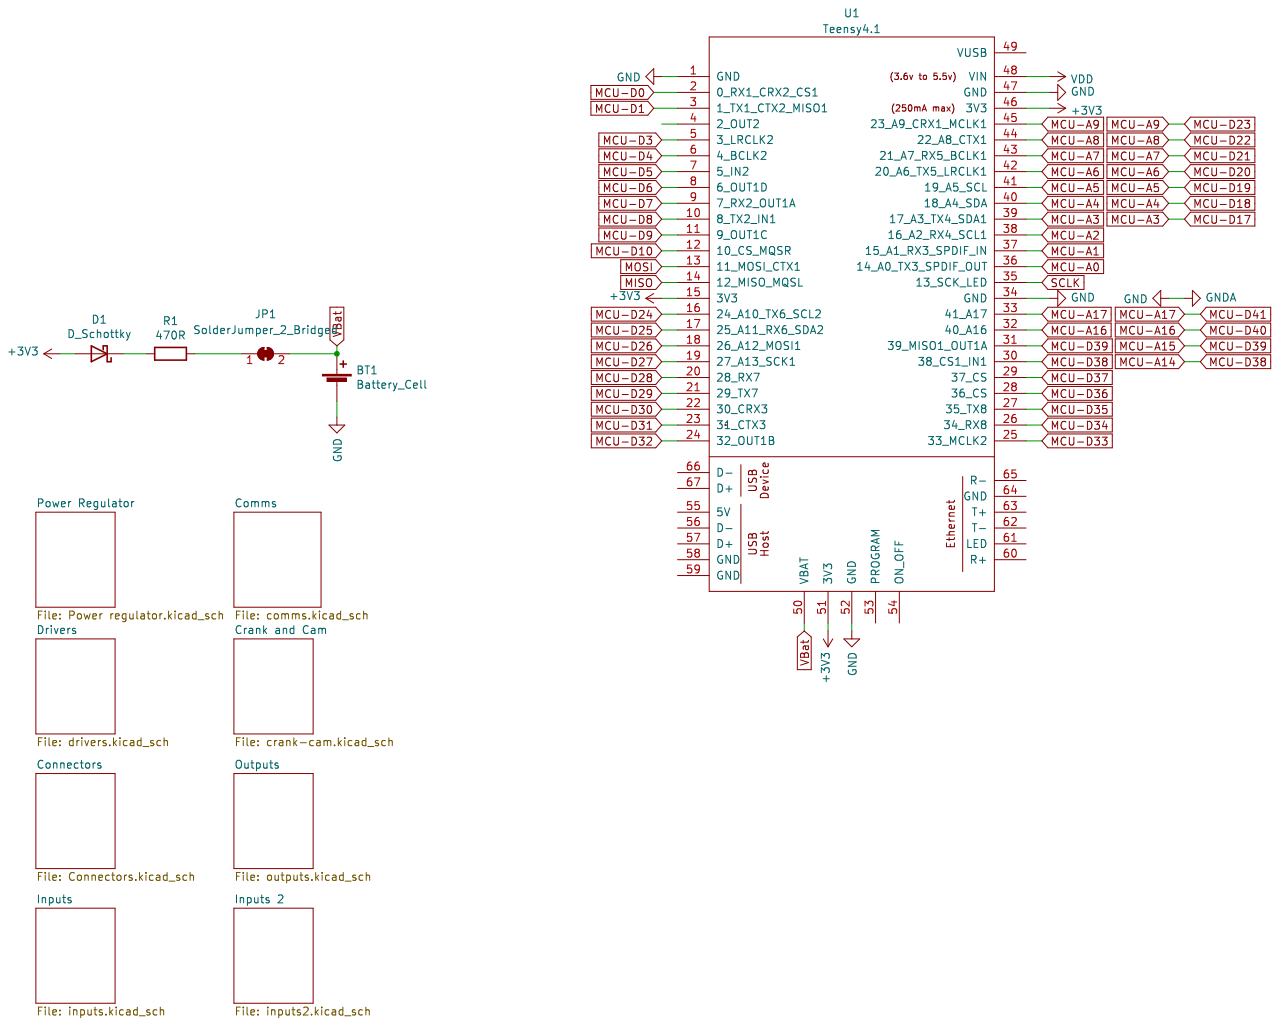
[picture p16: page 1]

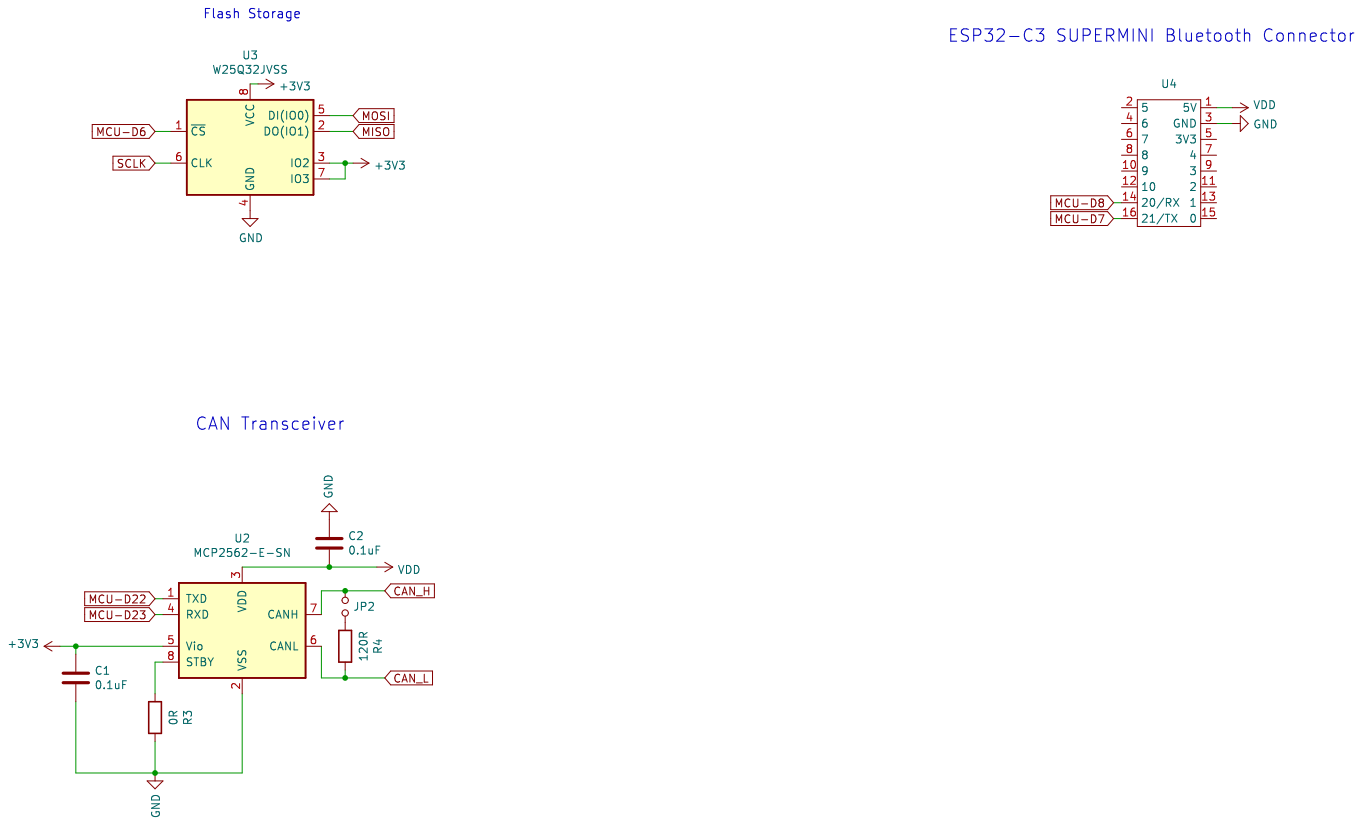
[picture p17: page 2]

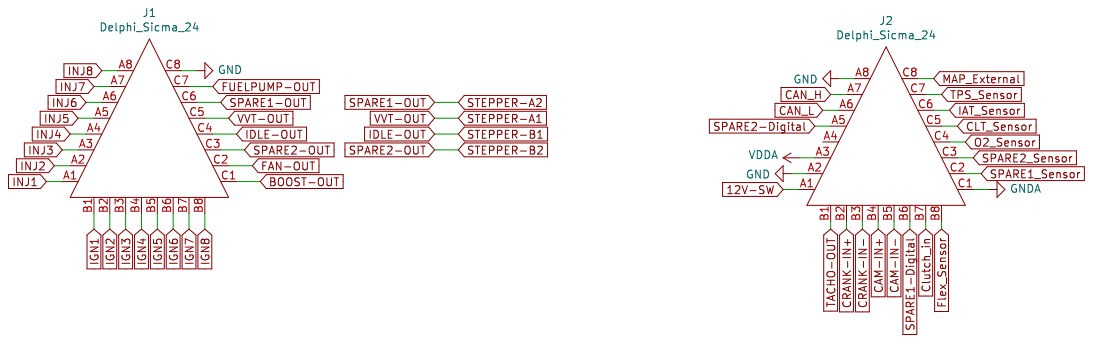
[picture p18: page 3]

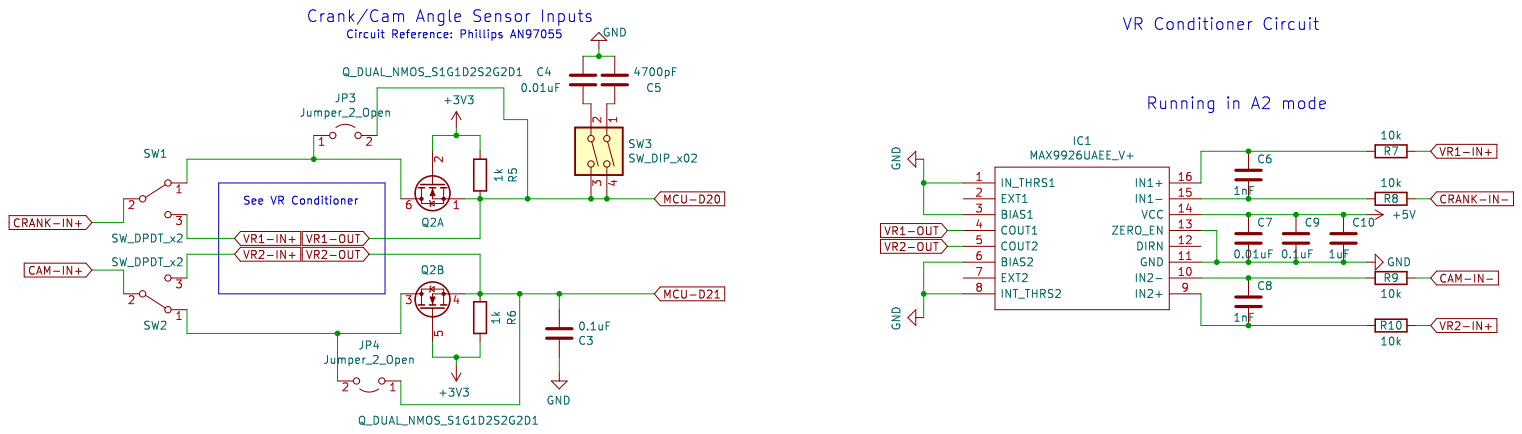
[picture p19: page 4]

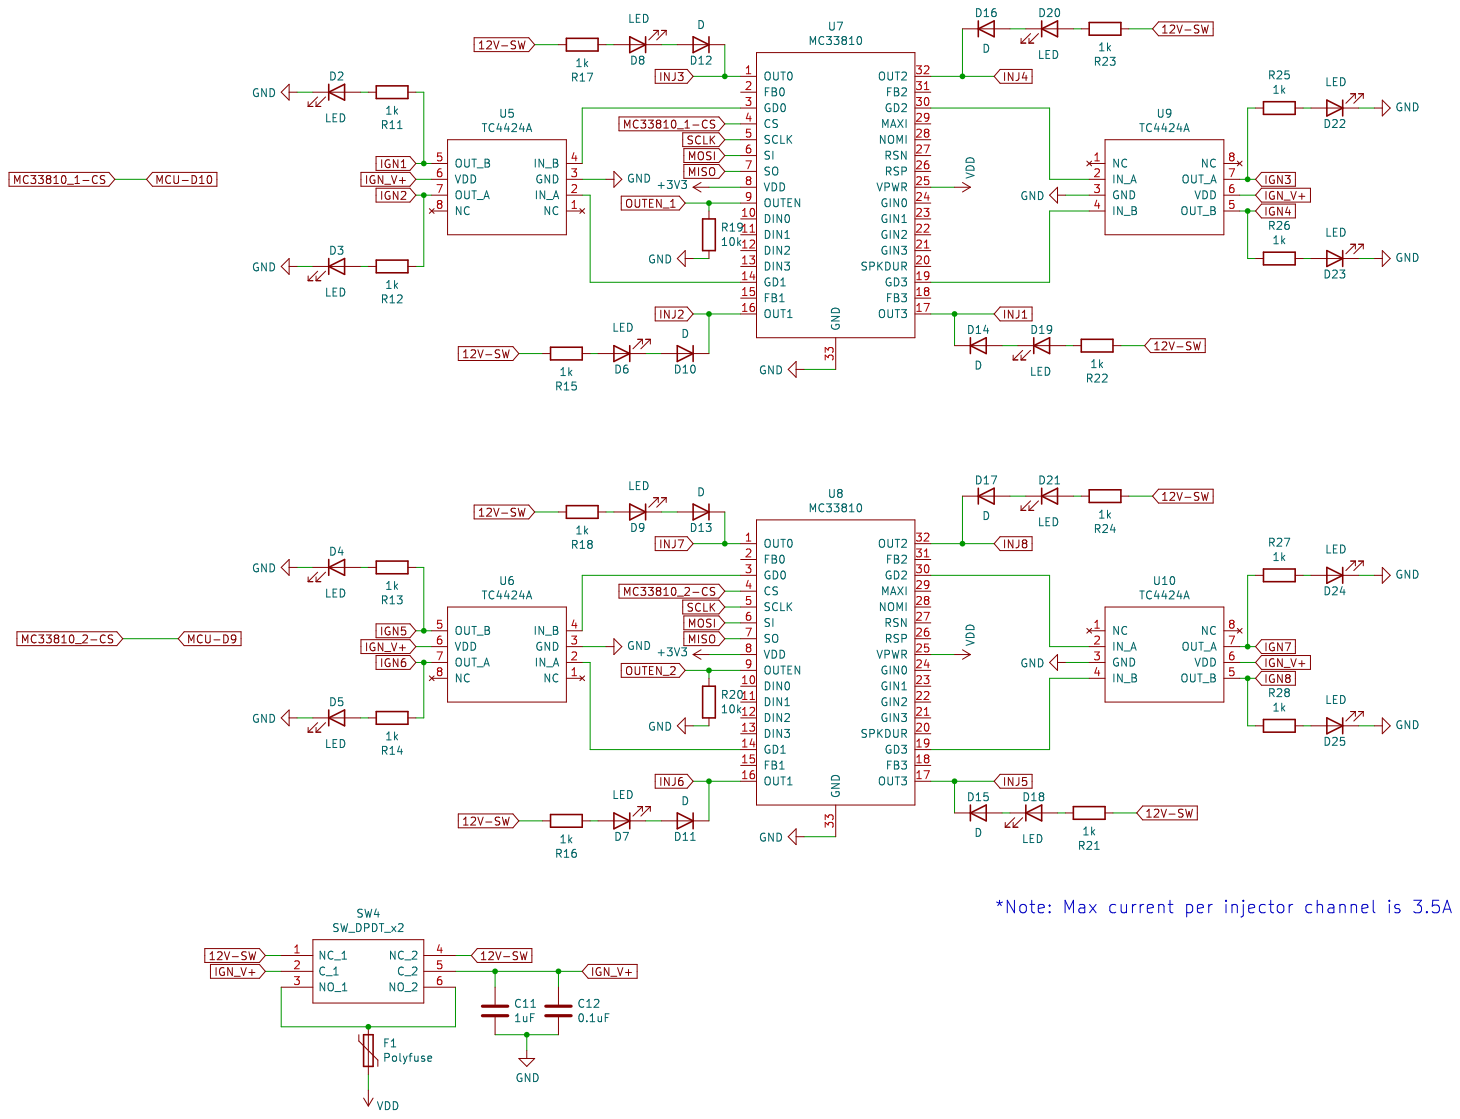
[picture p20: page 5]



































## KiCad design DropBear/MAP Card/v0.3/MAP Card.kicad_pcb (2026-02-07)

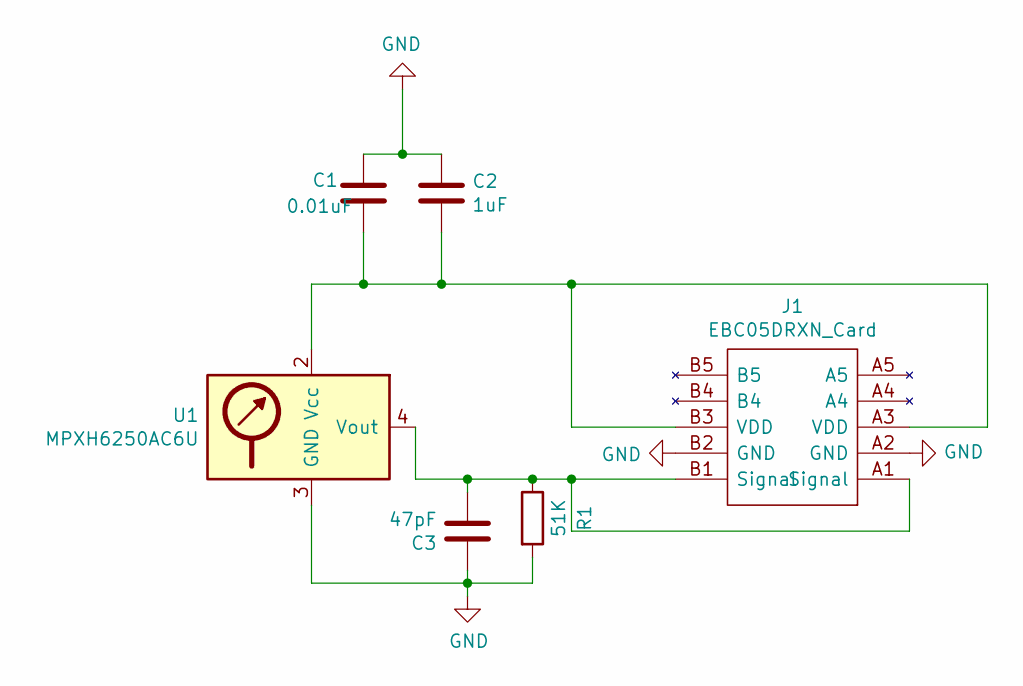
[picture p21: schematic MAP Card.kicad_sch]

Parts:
C1: 0.01uF; C_0805_2012Metric; Manufacturer_Part_Number CC0805KRX7R9BB103; Digikey Part Number 311-1136-1-ND
C2: 1uF; C_0805_2012Metric; Manufacturer_Part_Number CC0805KKX7R7BB105; Digikey Part Number 311-1365-1-ND
C3: 47pF; C_0805_2012Metric; Manufacturer_Part_Number C0805C470J5GACAUTO; Digikey Part Number 399-6963-1-ND
J1: EBC05DRXN_Card; Sullins_EBC05DRXN_2x05_P2.54mm_Edge; Manufacturer_Part_Number EBC05DRXN
R1: 51K; R_0805_2012Metric; Manufacturer_Part_Number RC0805FR-0751KL; Digikey Part Number 311-51.0KCRCT-ND
U1: MPXH6250AC6U; Manufacturer_Part_Number MPXH6250AC6U; Digikey Part Number MPXH6250AC6U-ND

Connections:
GND: C1.1, C2.1, C3.1, J1.A2 (GND), J1.B2 (GND), R1.2, U1.3 (GND)
unnamed: C1.2, C2.2, J1.A3 (VDD), J1.B3 (VDD), U1.2 (Vcc)
unnamed: C3.2, J1.A1 (Signal), J1.B1 (Signal), R1.1, U1.4 (Vout)

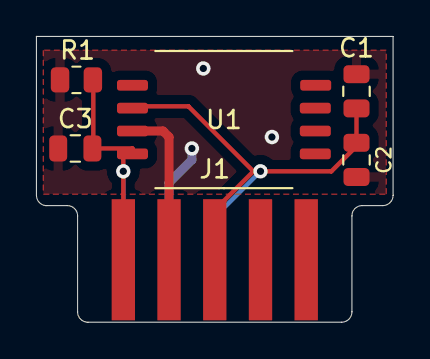
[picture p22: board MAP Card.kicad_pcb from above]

Board: 2 copper layers, 19.8 x 15.9 mm, 6 parts (0 on the bottom side), 3 nets.

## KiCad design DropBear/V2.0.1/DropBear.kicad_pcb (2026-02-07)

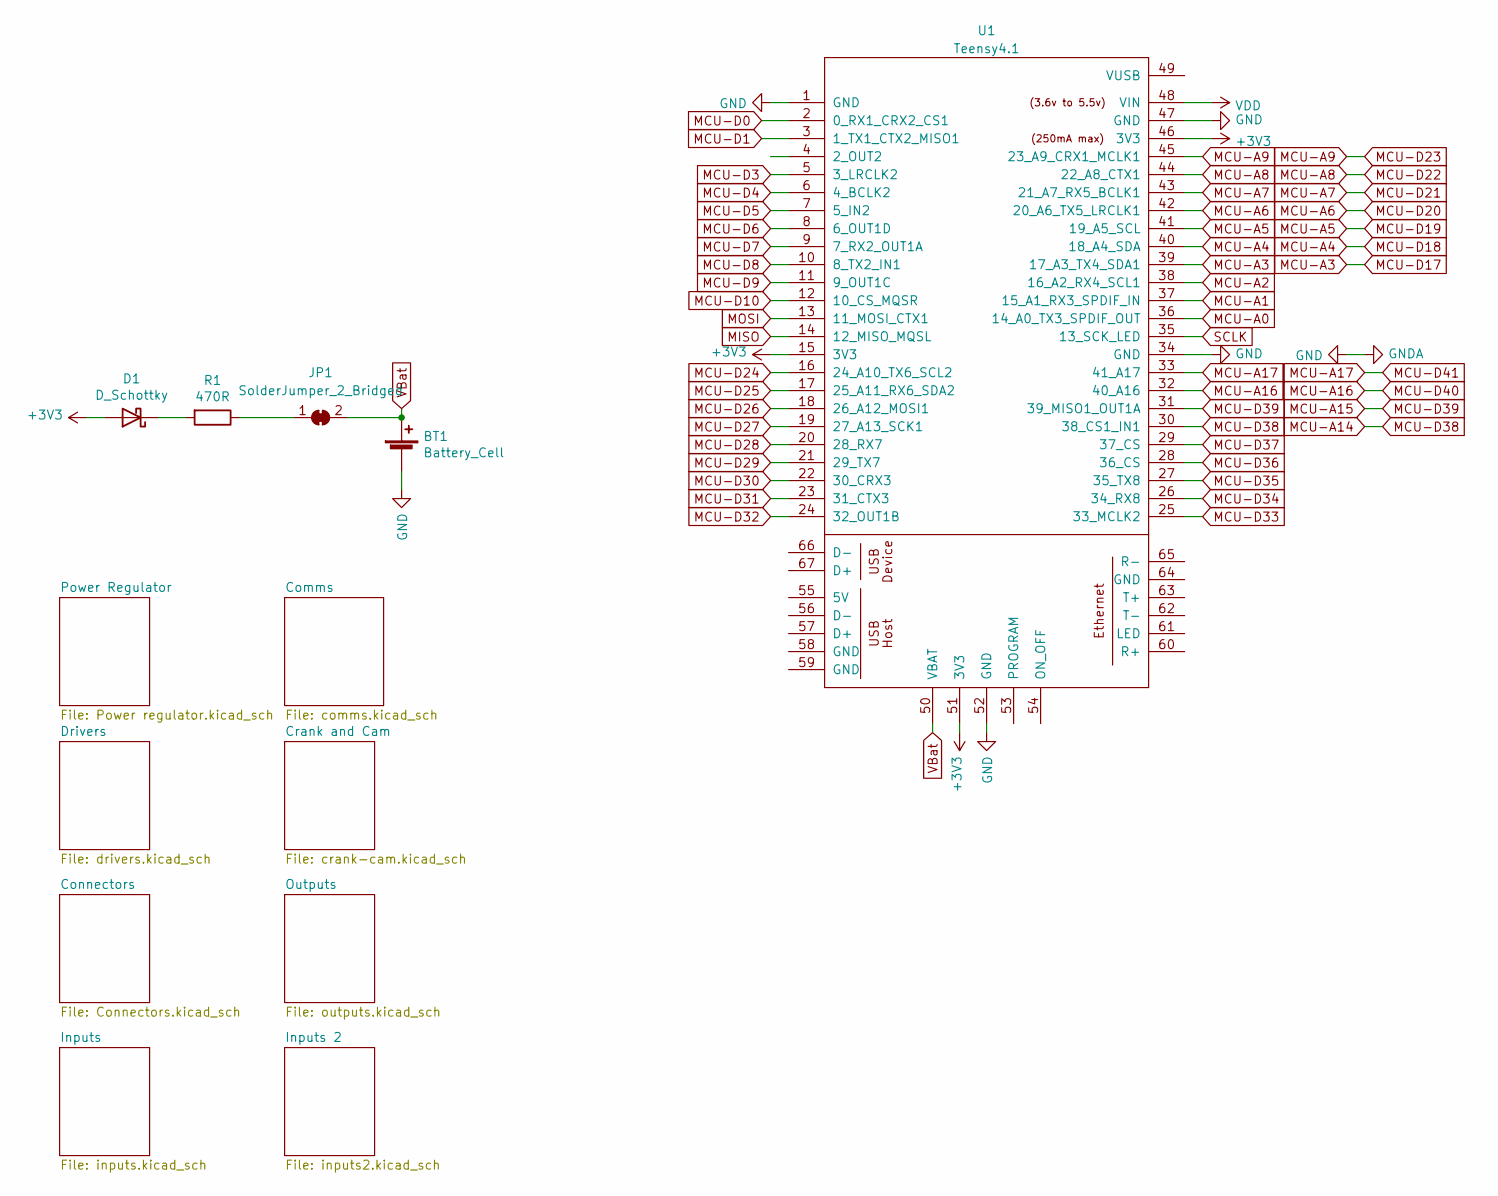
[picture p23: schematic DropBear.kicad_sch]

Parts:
BT1: Battery_Cell; BatteryHolder_Keystone_500; Manufacturer_Part_Number 500; Digikey Part Number 36-500-ND
D1: D_Schottky; D_PowerDI-123; Manufacturer_Part_Number DFLS2100-7; Digikey Part Number DFLS2100-7DICT-ND
JP1: SolderJumper_2_Bridged; SolderJumper-2_P1.3mm_Bridged_Pad1.0x1.5mm
R1: 470R; R_0805_2012Metric; Manufacturer_Part_Number ERJ-6ENF4700V; Digikey Part Number P470CCT-ND
U1: Teensy4.1; Teensy41

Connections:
+3V3: D1.2 (A), U1.15 (3V3), U1.46 (3V3), U1.51 (3V3); also elsewhere on the board
+5V: U1.48 (VIN); also elsewhere on the board
ADC-Clamp-1: U1.36 (14_A0_TX3_SPDIF_OUT); also elsewhere on the board
ADC-Clamp-4: U1.32 (40_A16); also elsewhere on the board
ADC-Clamp-5: U1.29 (37_CS); also elsewhere on the board
ADC-Clamp-6: U1.28 (36_CS); also elsewhere on the board
ADC-Clamp-7: U1.31 (39_MISO1_OUT1A); also elsewhere on the board
ADC-Clamp-10: U1.33 (41_A17); also elsewhere on the board
ADC-Clamp-12: U1.37 (15_A1_RX3_SPDIF_IN); also elsewhere on the board
ADC-Clamp-13: U1.38 (16_A2_RX4_SCL1); also elsewhere on the board
ADC-Clamp-14: U1.39 (17_A3_TX4_SDA1); also elsewhere on the board
GND: BT1.2 (-), U1.1 (GND), U1.34 (GND), U1.47 (GND), U1.52 (GND); also elsewhere on the board
MC33810_1-CS: U1.12 (10_CS_MQSR); also elsewhere on the board
MC33810_2-CS: U1.11 (9_OUT1C); also elsewhere on the board
MCU-A4: U1.40 (18_A4_SDA); also elsewhere on the board
MCU-A5: U1.41 (19_A5_SCL); also elsewhere on the board
MCU-A6: U1.42 (20_A6_TX5_LRCLK1); also elsewhere on the board
MCU-A7: U1.43 (21_A7_RX5_BCLK1); also elsewhere on the board
MCU-A8: U1.44 (22_A8_CTX1); also elsewhere on the board
MCU-A9: U1.45 (23_A9_CRX1_MCLK1); also elsewhere on the board
MCU-A14: U1.30 (38_CS1_IN1)
MCU-D0: U1.2 (0_RX1_CRX2_CS1); also elsewhere on the board
MCU-D1: U1.3 (1_TX1_CTX2_MISO1)
MCU-D3: U1.5 (3_LRCLK2)
MCU-D4: U1.6 (4_BCLK2)
MCU-D5: U1.7 (5_IN2); also elsewhere on the board
MCU-D6: U1.8 (6_OUT1D); also elsewhere on the board
MCU-D7: U1.9 (7_RX2_OUT1A); also elsewhere on the board
MCU-D8: U1.10 (8_TX2_IN1); also elsewhere on the board
MCU-D24: U1.16 (24_A10_TX6_SCL2); also elsewhere on the board
MCU-D25: U1.17 (25_A11_RX6_SDA2); also elsewhere on the board
MCU-D26: U1.18 (26_A12_MOSI1); also elsewhere on the board
MCU-D27: U1.19 (27_A13_SCK1); also elsewhere on the board
MCU-D28: U1.20 (28_RX7); also elsewhere on the board
MCU-D29: U1.21 (29_TX7); also elsewhere on the board
MCU-D30: U1.22 (30_CRX3); also elsewhere on the board
MCU-D31: U1.23 (31_CTX3); also elsewhere on the board
MCU-D32: U1.24 (32_OUT1B); also elsewhere on the board
MCU-D33: U1.25 (33_MCLK2)
MCU-D34: U1.26 (34_RX8); also elsewhere on the board
MCU-D35: U1.27 (35_TX8); also elsewhere on the board
MISO: U1.14 (12_MISO_MQSL); also elsewhere on the board
MOSI: U1.13 (11_MOSI_CTX1); also elsewhere on the board
unnamed: D1.1 (K), R1.2
unnamed: JP1.1 (A), R1.1
SCLK: U1.35 (13_SCK_LED); also elsewhere on the board
VBat: BT1.1 (+), JP1.2 (B), U1.50 (VBAT)

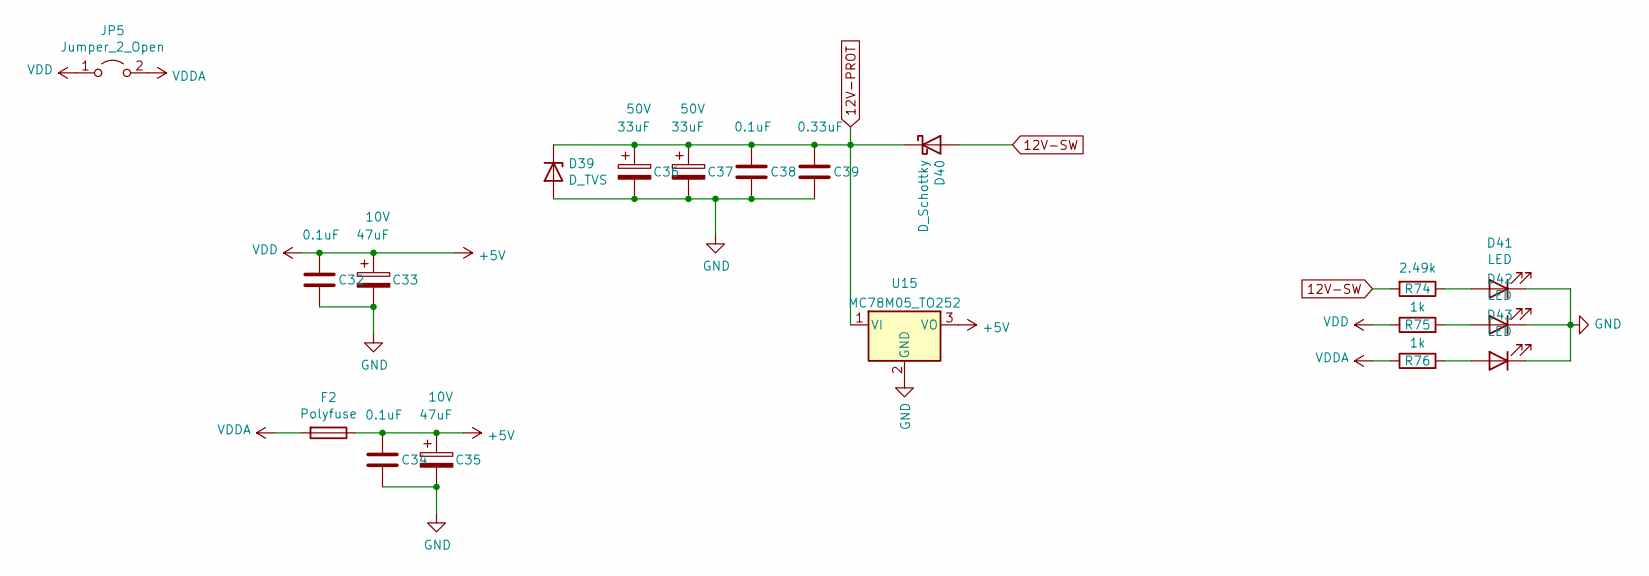
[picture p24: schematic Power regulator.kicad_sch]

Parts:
C32, C34, C38: 0.1uF; C_0805_2012Metric; Manufacturer_Part_Number CC0805KRX7R9BB104; Digikey Part Number 311-1140-1-ND
C33, C35: 47uF; CP_EIA-3528-21_Kemet-B; Voltage 10V; Manufacturer_Part_Number TAJB476K006RNJ; Digikey Part Number 478-1692-1-ND
C36, C37: 33uF; CP_Elec_6.3x7.7; Voltage 50V; Manufacturer_Part_Number EEE-1HA330XP; Digikey Part Number PCE3925CT-ND
C39: 0.33uF; C_0805_2012Metric; Manufacturer_Part_Number CGA4J2X7R1H334K125AA; Digikey Part Number 445-5684-1-ND
D39: D_TVS; D_SMB; Manufacturer_Part_Number SMBJ40A-Q; Digikey Part Number SMBJ40A-QCT-ND
D40: D_Schottky; D_SMA_Handsoldering; Manufacturer_Part_Number B360A-13-F; Digikey Part Number B360A-FDICT-ND
D41, D42, D43: LED; LED_0805_2012Metric; Manufacturer_Part_Number LG R971-KN-1; Digikey Part Number 475-1410-2-ND
F2: Polyfuse; Fuse_0603_1608Metric; Manufacturer_Part_Number 0ZCM0008FF2G; Digikey Part Number 507-1817-1-ND
JP5: Jumper_2_Open; SolderJumper-2_P1.3mm_Open_Pad1.0x1.5mm
R74: 2.49k; R_0805_2012Metric; Tolerance 0.1%; Manufacturer_Part_Number RT0805BRD072K49L; Digikey Part Number YAG1854CT-ND
R75, R76: 1k; R_0805_2012Metric; Manufacturer_Part_Number RC0805FR-071KL; Digikey Part Number 311-1.00KCRCT-ND
U15: MC78M05_TO252; TO-252-2; Manufacturer_Part_Number NCV7805BDTRKG; Digikey Part Number NCV7805BDTRKGOSCT-ND

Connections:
12V-PROT: C36.1, C37.1, C38.1, C39.1, D39.1 (K), D40.1 (K), U15.1 (VI)
12V-SW: D40.2 (A), R74.2; also elsewhere on the board
+5V: C32.1, C33.1, C34.1, C35.1, F2.1, JP5.1 (A), R75.1, U15.3 (VO); also elsewhere on the board
GND: C32.2, C33.2, C34.2, C35.2, C36.2, C37.2, C38.2, C39.2, D39.2 (A), D41.1 (K), D42.1 (K), D43.1 (K), U15.2 (GND); also elsewhere on the board
unnamed: D41.2 (A), R74.1
unnamed: D42.2 (A), R75.2
unnamed: D43.2 (A), R76.2
VDDA: F2.2, JP5.2 (B), R76.1; also elsewhere on the board

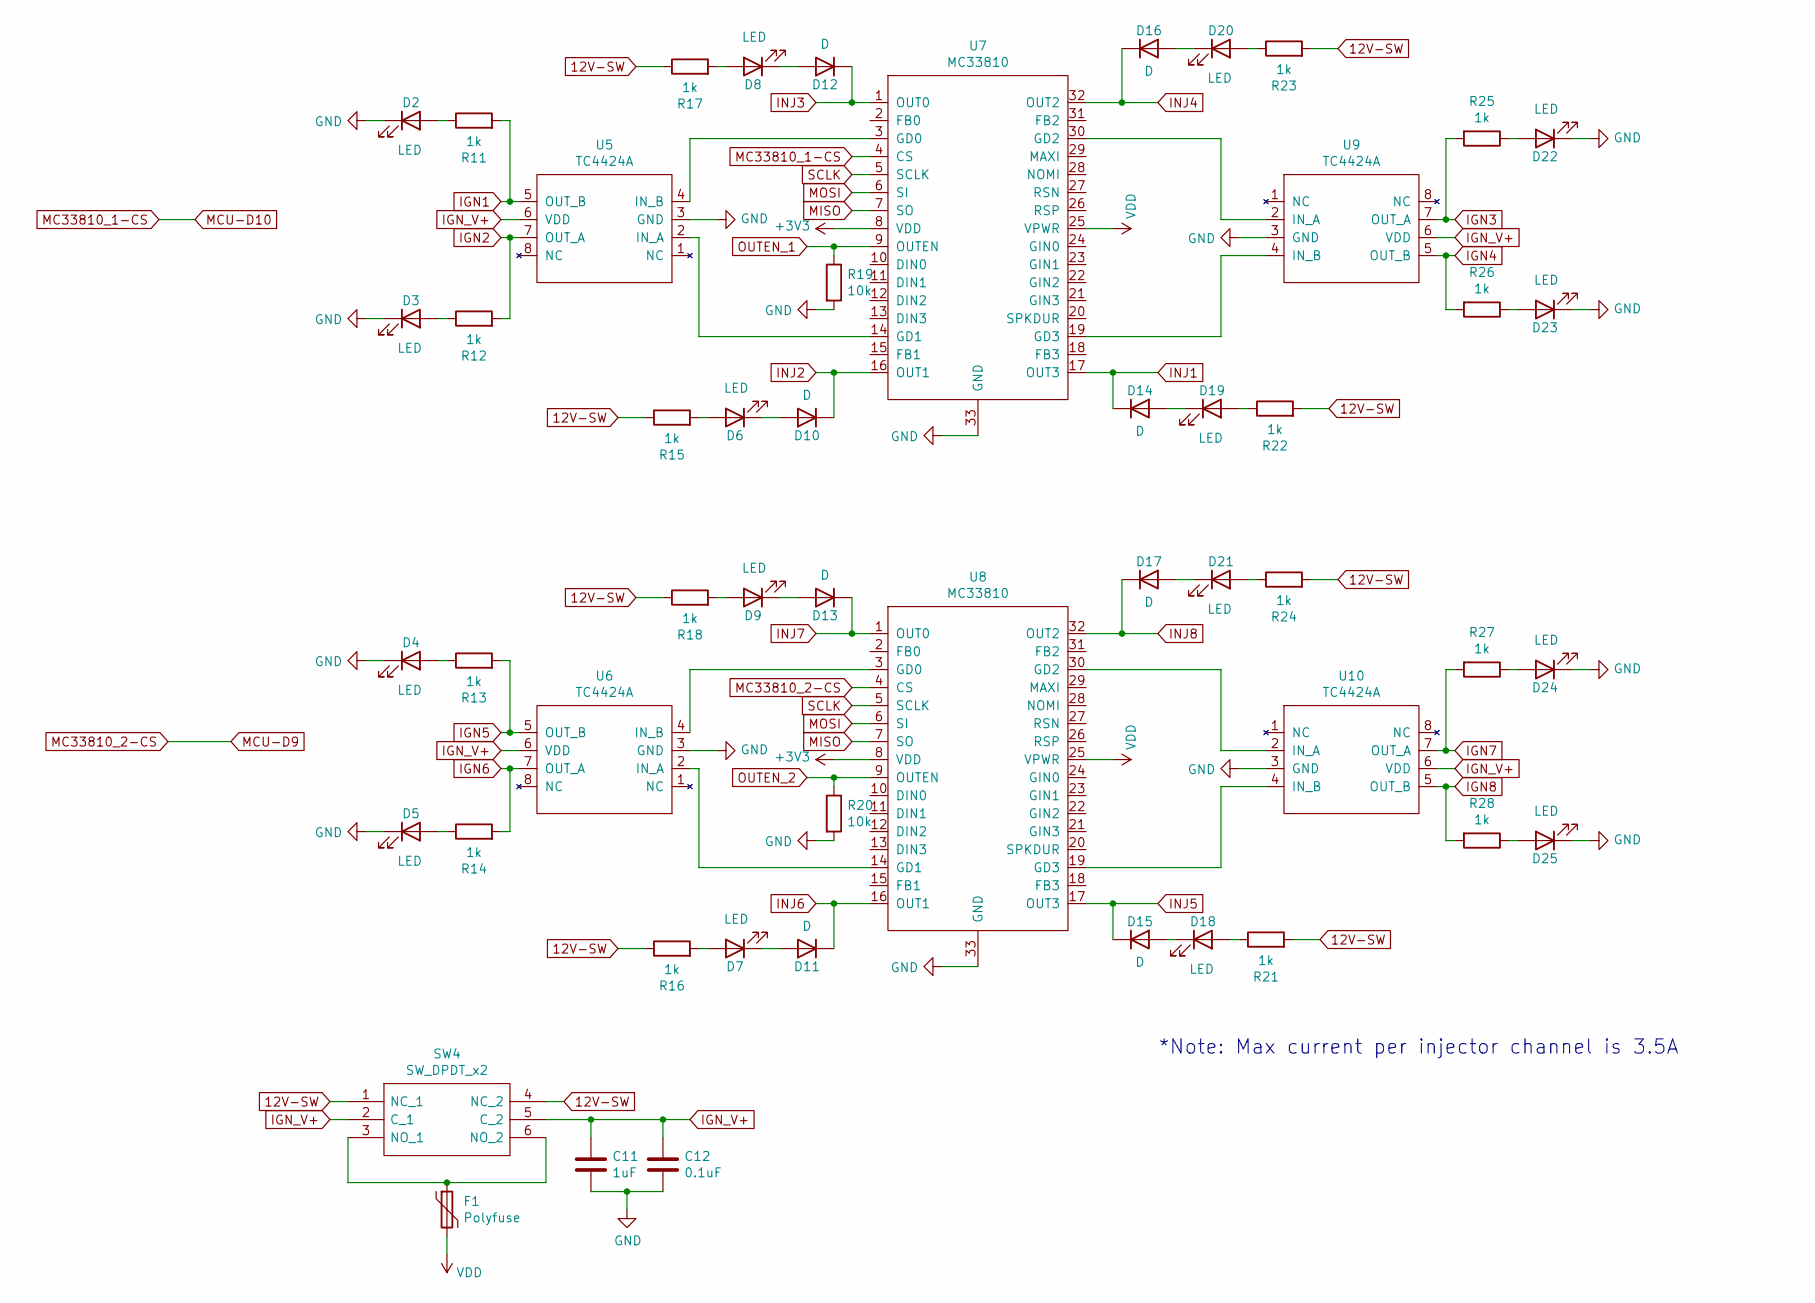
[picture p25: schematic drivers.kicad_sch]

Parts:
C11: 1uF; C_0805_2012Metric; Manufacturer_Part_Number CC0805KKX7R7BB105; Digikey Part Number 311-1365-1-ND
C12: 0.1uF; C_0805_2012Metric; Manufacturer_Part_Number CC0805KRX7R9BB104; Digikey Part Number 311-1140-1-ND
D2, D3, D4, D5, D22, D23, D24, D25: LED; LED_0805_2012Metric; Manufacturer_Part_Number SML-H12D8TT86C; Digikey Part Number SML-H12D8TT86CCT-ND
D6, D7, D8, D9, D18, D19, D20, D21: LED; LED_0805_2012Metric; Manufacturer_Part_Number LH R974-LP-1; Digikey Part Number 475-1415-1-ND
D10, D11, D12, D13, D14, D15, D16, D17: D; D_SOD-323; Manufacturer_Part_Number 1N4448WX-TP; Digikey Part Number 1N4448WXTPMSCT-ND
F1: Polyfuse; Fuse_1812_4532Metric; Manufacturer_Part_Number 0ZCC0050FF2C; Digikey Part Number 507-1361-1-ND
R11, R12, R13, R14, R15, R16, R17, R18, R21, R22, R23, R24, R25, R26, R27, R28: 1k; R_0805_2012Metric; Manufacturer_Part_Number RC0805FR-071KL; Digikey Part Number 311-1.00KCRCT-ND
R19, R20: 10k; R_0805_2012Metric; Manufacturer_Part_Number RC0805JR-0710KL; Digikey Part Number 311-10KARCT-ND
SW4: SW_DPDT_x2; AYZ0202AGRLC; Manufacturer_Part_Number AYZ0202AGRLC; Digikey Part Number 401-2013-1-ND
U5, U6, U9, U10: TC4424A; SOIC-8_3.9x4.9mm_P1.27mm; Manufacturer_Part_Number TC4424AVOA; Digikey Part Number TC4424AVOA-ND
U7, U8: MC33810; SOIC32-P0.65-33N; Manufacturer_Part_Number MCZ33810EK

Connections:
12V-SW: R15.1, R16.1, R17.1, R18.1, R21.2, R22.2, R23.2, R24.2, SW4.1 (NC_1), SW4.4 (NC_2); also elsewhere on the board
+3V3: U7.8 (VDD), U8.8 (VDD); also elsewhere on the board
+5V: F1.2, U7.25 (VPWR), U8.25 (VPWR); also elsewhere on the board
GND: C11.2, C12.2, D2.1 (K), D3.1 (K), D4.1 (K), D5.1 (K), D22.1 (K), D23.1 (K), D24.1 (K), D25.1 (K), R19.2, R20.2, U5.3 (GND), U6.3 (GND), U7.33 (GND), U8.33 (GND), U9.3 (GND), U10.3 (GND); also elsewhere on the board
IGN1: R11.2, U5.5 (OUT_B); also elsewhere on the board
IGN2: R12.2, U5.7 (OUT_A); also elsewhere on the board
IGN3: R25.2, U9.7 (OUT_A); also elsewhere on the board
IGN4: R26.2, U9.5 (OUT_B); also elsewhere on the board
IGN5: R13.2, U6.5 (OUT_B); also elsewhere on the board
IGN6: R14.2, U6.7 (OUT_A); also elsewhere on the board
IGN7: R27.2, U10.7 (OUT_A); also elsewhere on the board
IGN8: R28.2, U10.5 (OUT_B); also elsewhere on the board
IGN_V+: C11.1, C12.1, SW4.2 (C_1), SW4.5 (C_2), U5.6 (VDD), U6.6 (VDD), U9.6 (VDD), U10.6 (VDD)
INJ1: D14.1 (K), U7.17 (OUT3); also elsewhere on the board
INJ2: D10.1 (K), U7.16 (OUT1); also elsewhere on the board
INJ3: D12.1 (K), U7.1 (OUT0); also elsewhere on the board
INJ4: D16.1 (K), U7.32 (OUT2); also elsewhere on the board
INJ5: D15.1 (K), U8.17 (OUT3); also elsewhere on the board
INJ6: D11.1 (K), U8.16 (OUT1); also elsewhere on the board
INJ7: D13.1 (K), U8.1 (OUT0); also elsewhere on the board
INJ8: D17.1 (K), U8.32 (OUT2); also elsewhere on the board
MC33810_1-CS: U7.4 (CS); also elsewhere on the board
MC33810_2-CS: U8.4 (CS); also elsewhere on the board
MISO: U7.7 (SO), U8.7 (SO); also elsewhere on the board
MOSI: U7.6 (SI), U8.6 (SI); also elsewhere on the board
unnamed: D2.2 (A), R11.1
unnamed: D3.2 (A), R12.1
unnamed: D4.2 (A), R13.1
unnamed: D5.2 (A), R14.1
unnamed: D6.2 (A), R15.2
unnamed: D7.2 (A), R16.2
unnamed: D8.2 (A), R17.2
unnamed: D9.2 (A), R18.2
unnamed: D6.1 (K), D10.2 (A)
unnamed: D7.1 (K), D11.2 (A)
unnamed: D8.1 (K), D12.2 (A)
unnamed: D9.1 (K), D13.2 (A)
unnamed: D14.2 (A), D19.1 (K)
unnamed: D15.2 (A), D18.1 (K)
unnamed: D16.2 (A), D20.1 (K)
unnamed: D17.2 (A), D21.1 (K)
unnamed: D18.2 (A), R21.1
unnamed: D19.2 (A), R22.1
unnamed: D20.2 (A), R23.1
unnamed: D21.2 (A), R24.1
unnamed: D22.2 (A), R25.1
unnamed: D23.2 (A), R26.1
unnamed: D24.2 (A), R27.1
unnamed: D25.2 (A), R28.1
unnamed: F1.1, SW4.3 (NO_1), SW4.6 (NO_2)
unnamed: U5.2 (IN_A), U7.14 (GD1)
unnamed: U5.4 (IN_B), U7.3 (GD0)
unnamed: U6.2 (IN_A), U8.14 (GD1)
unnamed: U6.4 (IN_B), U8.3 (GD0)
unnamed: U7.30 (GD2), U9.2 (IN_A)
unnamed: U7.19 (GD3), U9.4 (IN_B)
unnamed: U8.30 (GD2), U10.2 (IN_A)
unnamed: U8.19 (GD3), U10.4 (IN_B)
OUTEN_1: R19.1, U7.9 (OUTEN)
OUTEN_2: R20.1, U8.9 (OUTEN)
SCLK: U7.5 (SCLK), U8.5 (SCLK); also elsewhere on the board

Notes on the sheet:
*Note: Max current per injector channel is 3.5A

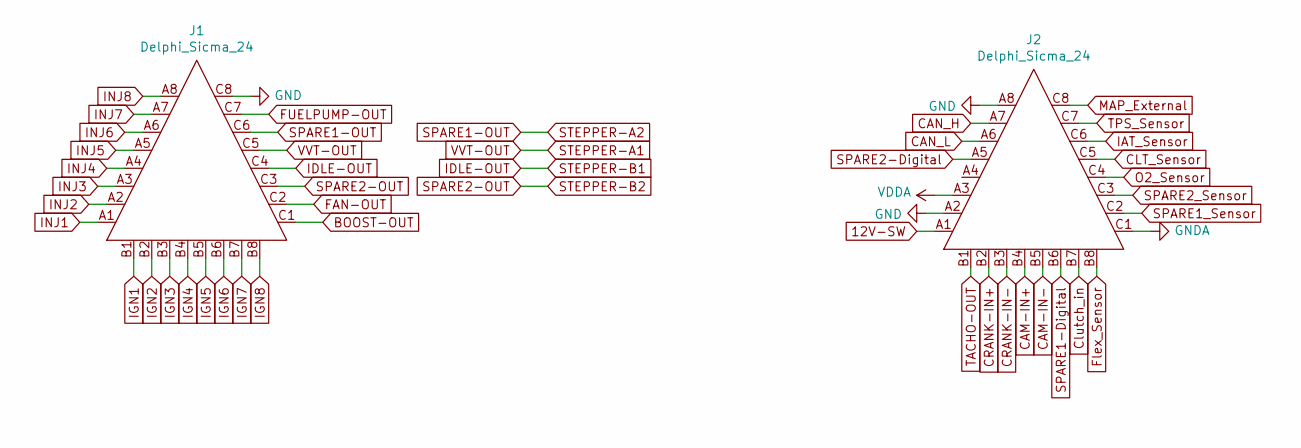
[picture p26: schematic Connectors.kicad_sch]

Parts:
J1: Delphi_Sicma_24; Delphi_Sicma_24_Grey
J2: Delphi_Sicma_24; Delphi_Sicma_24_Black

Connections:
12V-SW: J2.A1; also elsewhere on the board
ADC-Clamp-5: J2.B8; also elsewhere on the board
ADC-Clamp-6: J2.B7; also elsewhere on the board
BOOST-OUT: J1.C1; also elsewhere on the board
CAM-IN+: J2.B4; also elsewhere on the board
CAM-IN-: J2.B5; also elsewhere on the board
CAN_H: J2.A7; also elsewhere on the board
CAN_L: J2.A6; also elsewhere on the board
CLT_Sensor: J2.C5; also elsewhere on the board
CRANK-IN+: J2.B2; also elsewhere on the board
CRANK-IN-: J2.B3; also elsewhere on the board
FAN-OUT: J1.C2; also elsewhere on the board
FUELPUMP-OUT: J1.C7; also elsewhere on the board
GND: J1.C8, J2.A2, J2.A8, J2.C1; also elsewhere on the board
IAT_Sensor: J2.C6; also elsewhere on the board
IDLE-OUT: J1.C4; also elsewhere on the board
IGN1: J1.B1; also elsewhere on the board
IGN2: J1.B2; also elsewhere on the board
IGN3: J1.B3; also elsewhere on the board
IGN4: J1.B4; also elsewhere on the board
IGN5: J1.B5; also elsewhere on the board
IGN6: J1.B6; also elsewhere on the board
IGN7: J1.B7; also elsewhere on the board
IGN8: J1.B8; also elsewhere on the board
INJ1: J1.A1; also elsewhere on the board
INJ2: J1.A2; also elsewhere on the board
INJ3: J1.A3; also elsewhere on the board
INJ4: J1.A4; also elsewhere on the board
INJ5: J1.A5; also elsewhere on the board
INJ6: J1.A6; also elsewhere on the board
INJ7: J1.A7; also elsewhere on the board
INJ8: J1.A8; also elsewhere on the board
MAP_External: J2.C8; also elsewhere on the board
O2_Sensor: J2.C4; also elsewhere on the board
SPARE1-Digital: J2.B6; also elsewhere on the board
SPARE1-OUT: J1.C6; also elsewhere on the board
SPARE1_Sensor: J2.C2; also elsewhere on the board
SPARE2-Digital: J2.A5; also elsewhere on the board
SPARE2-OUT: J1.C3; also elsewhere on the board
SPARE2_Sensor: J2.C3; also elsewhere on the board
STEPPER-A1: J1.C5; also elsewhere on the board
TACHO-OUT: J2.B1; also elsewhere on the board
TPS_Sensor: J2.C7; also elsewhere on the board
VDDA: J2.A3; also elsewhere on the board

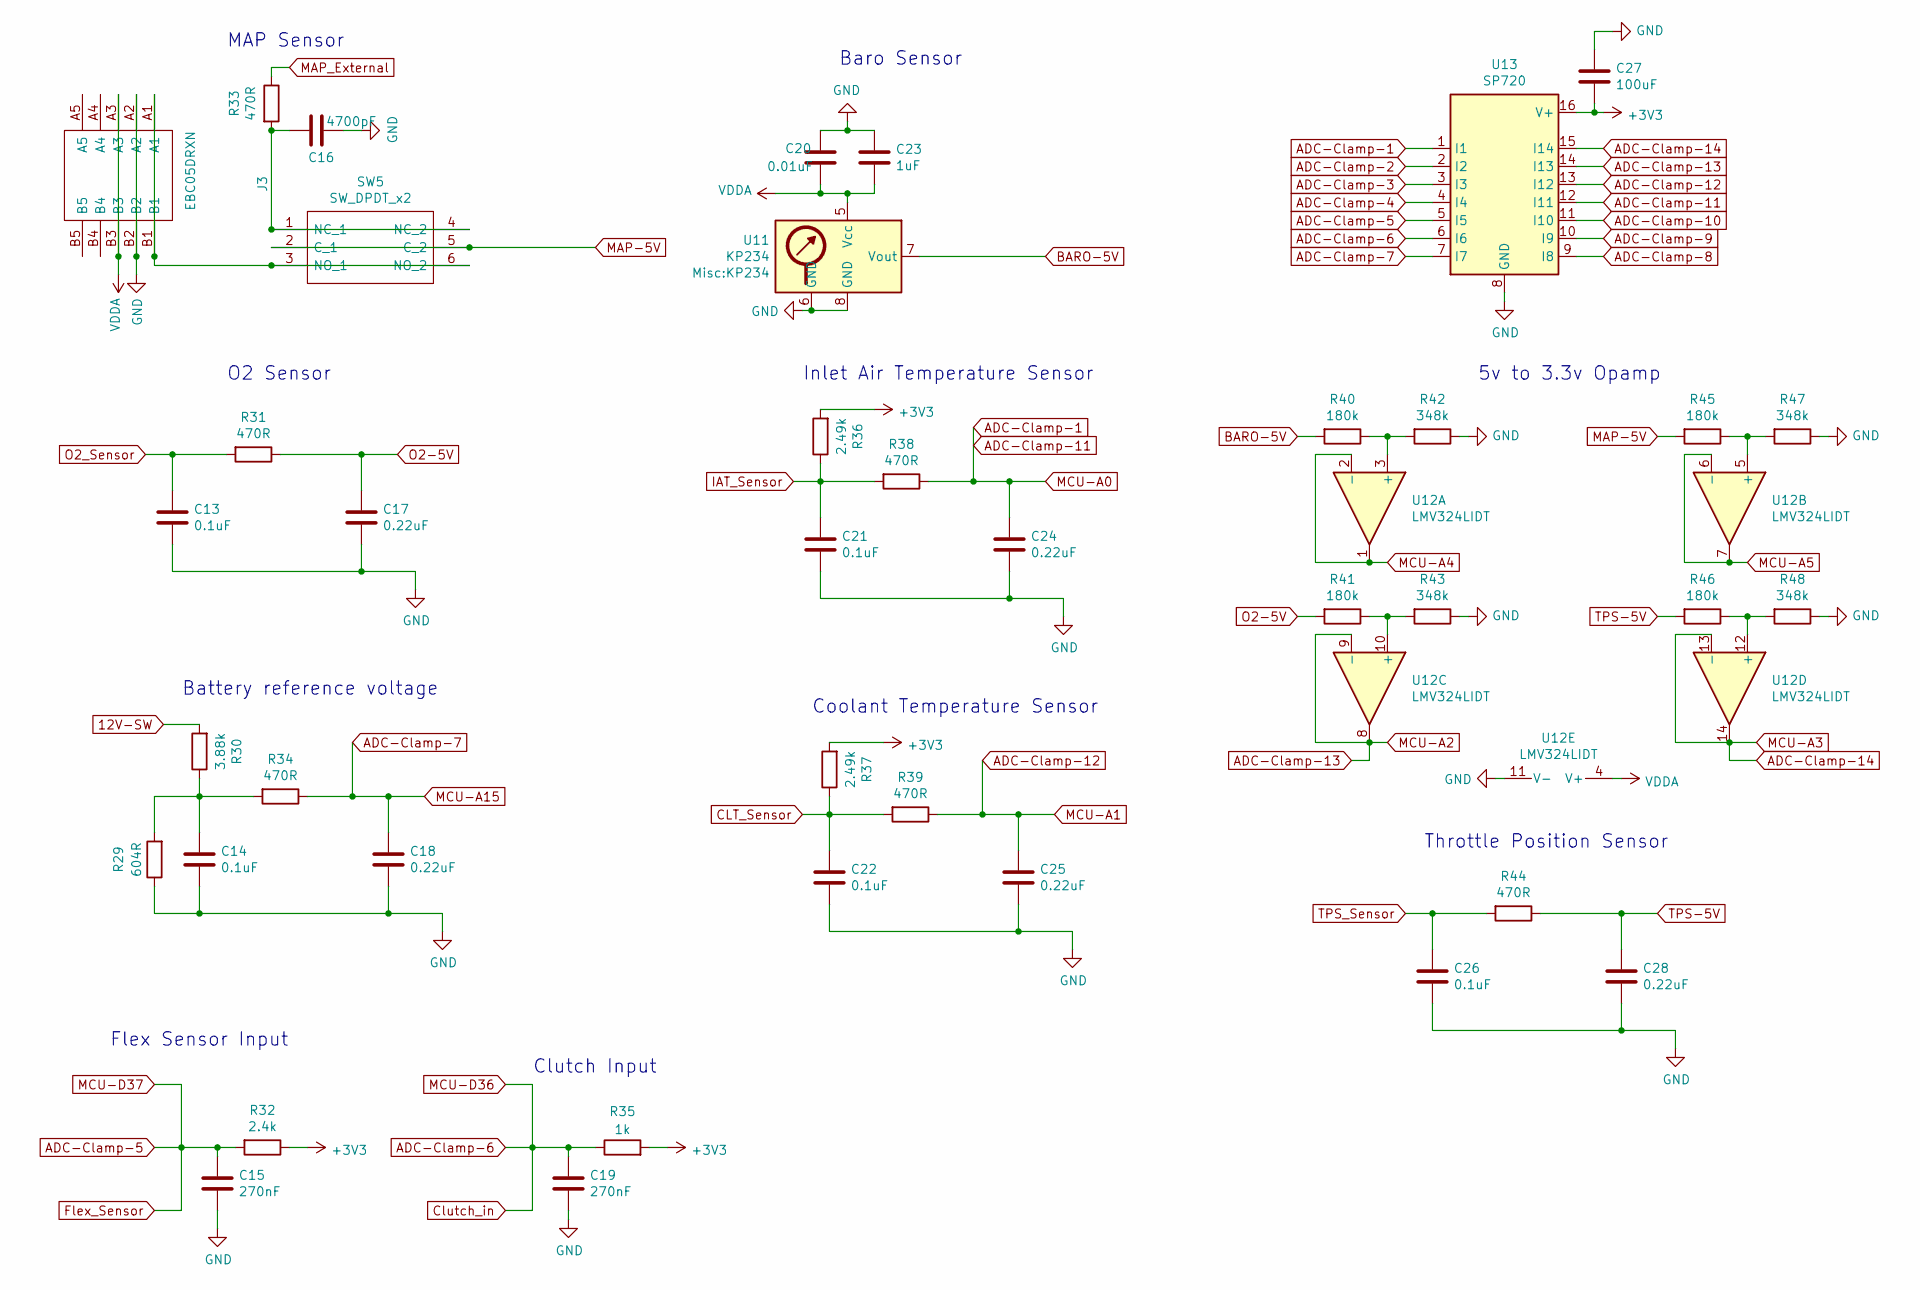
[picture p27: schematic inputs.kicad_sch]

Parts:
C13, C14, C21, C22, C26: 0.1uF; C_0805_2012Metric; Manufacturer_Part_Number CC0805KRX7R9BB104; Digikey Part Number 311-1140-1-ND
C15, C19: 270nF; C_0805_2012Metric; Manufacturer_Part_Number CC0805JRX7R7BB274; Digikey Part Number 311-4268-1-ND
C16: 4700pF; C_0805_2012Metric; Manufacturer_Part_Number CC0805KRX7R9BB472; Digikey Part Number 311-1133-1-ND
C17, C18, C24, C25, C28: 0.22uF; C_0805_2012Metric; Manufacturer_Part_Number CL21B224KOCNNNC; Digikey Part Number 1276-1284-1-ND
C20: 0.01uF; C_0805_2012Metric; Manufacturer_Part_Number CC0805KRX7R9BB103; Digikey Part Number 311-1136-1-ND
C23: 1uF; C_0805_2012Metric; Manufacturer_Part_Number CC0805KKX7R7BB105; Digikey Part Number 311-1365-1-ND
C27: 100uF; C_1206_3216Metric; Manufacturer_Part_Number CL31A107MQHNNNE; Digikey Part Number 1276-1782-1-ND
J3: EBC05DRXN; Manufacturer_Part_Number EBC05DRXN; Digikey Part Number S9641-ND
R29: 604R; R_0805_2012Metric; Tolerance 1%; Manufacturer_Part_Number RC0805FR-07604RL; Digikey Part Number 311-604CRCT-ND
R30: 3.88k; R_0603_1608Metric_Pad0.98x0.95mm_HandSolder; Tolerance 1%; Manufacturer_Part_Number RT0603BRD073K88L; Digikey Part Number YAG4550CT-ND
R31, R33, R34, R38, R39, R44: 470R; R_0805_2012Metric; Manufacturer_Part_Number ERJ-6ENF4700V; Digikey Part Number P470CCT-ND
R32: 2.4k; R_0805_2012Metric; Manufacturer_Part_Number RC0805FR-072K4L; Digikey Part Number 311-2.40KCRCT-ND
R35: 1k; R_0805_2012Metric; Manufacturer_Part_Number RC0805FR-071KL; Digikey Part Number 311-1.00KCRCT-ND
R36, R37: 2.49k; R_0805_2012Metric; Tolerance 0.1%; Manufacturer_Part_Number RT0805BRD072K49L; Digikey Part Number YAG1854CT-ND
R40, R41, R45, R46: 180k; R_0805_2012Metric; Manufacturer_Part_Number RC0805FR-07180KL; Digikey Part Number 311-180KCRCT-ND
R42, R43, R47, R48: 348k; R_0805_2012Metric; Manufacturer_Part_Number ERJ-6ENF3483V; Digikey Part Number P348KCDKR-ND
SW5: SW_DPDT_x2; AYZ0202AGRLC; Manufacturer_Part_Number AYZ0202AGRLC; Digikey Part Number 401-2013-1-ND
U11: KP234; Manufacturer_Part_Number KP234XTMA1; Digikey Part Number 448-KP234XTMA1CT-ND
U12: LMV324LIDT; SOIC-14_3.9x8.7mm_P1.27mm; Manufacturer_Part_Number LMV324LIDT; Digikey Part Number 497-13052-1-ND
U13: SP720; SOIC-16_3.9x9.9mm_P1.27mm; Manufacturer_Part_Number SP720ABTG; Digikey Part Number F3162CT-ND

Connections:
12V-SW: R30.2; also elsewhere on the board
+3V3: C27.2, R32.1, R35.2, R36.2, R37.2, U13.16 (V+); also elsewhere on the board
ADC-Clamp-1: C24.1, R38.1, U13.1 (I1), U13.12 (I11); also elsewhere on the board
ADC-Clamp-3: U13.3 (I3)
ADC-Clamp-4: U13.4 (I4); also elsewhere on the board
ADC-Clamp-5: C15.1, R32.2, U13.5 (I5); also elsewhere on the board
ADC-Clamp-6: C19.1, R35.1, U13.6 (I6); also elsewhere on the board
ADC-Clamp-7: C18.1, R34.1, U13.7 (I7); also elsewhere on the board
ADC-Clamp-8: U13.9 (I8)
ADC-Clamp-9: U13.10 (I9)
ADC-Clamp-10: U13.2 (I2), U13.11 (I10); also elsewhere on the board
ADC-Clamp-12: C25.1, R39.1, U13.13 (I12); also elsewhere on the board
ADC-Clamp-13: U12.8, U12.9 (-), U13.14 (I13); also elsewhere on the board
ADC-Clamp-14: U12.13 (-), U12.14, U13.15 (I14); also elsewhere on the board
BARO-5V: R40.2, U11.7 (Vout)
CLT_Sensor: C22.1, R37.1, R39.2; also elsewhere on the board
GND: C13.2, C14.2, C15.2, C16.1, C17.2, C18.2, C19.2, C20.1, C21.2, C22.2, C23.1, C24.2, C25.2, C26.2, C27.1, C28.2, J3.A2, J3.B2, R29.1, R42.1, R43.1, R47.1, R48.1, U11.6 (GND), U11.8 (GND), U12.11 (V-), U13.8 (GND); also elsewhere on the board
IAT_Sensor: C21.1, R36.1, R38.2; also elsewhere on the board
MAP-5V: R45.2, SW5.2 (C_1), SW5.5 (C_2)
MAP_External: R33.1; also elsewhere on the board
MCU-A4: U12.1, U12.2 (-); also elsewhere on the board
MCU-A5: U12.6 (-), U12.7; also elsewhere on the board
unnamed: C14.1, R29.2, R30.1, R34.2
unnamed: C16.2, R33.2, SW5.1 (NC_1), SW5.4 (NC_2)
unnamed: J3.A1, J3.B1, SW5.3 (NO_1), SW5.6 (NO_2)
unnamed: R40.1, R42.2, U12.3 (+)
unnamed: R45.1, R47.2, U12.5 (+)
unnamed: R41.1, R43.2, U12.10 (+)
unnamed: R46.1, R48.2, U12.12 (+)
O2-5V: C17.1, R31.1, R41.2
O2_Sensor: C13.1, R31.2; also elsewhere on the board
TPS-5V: C28.1, R44.1, R46.2
TPS_Sensor: C26.1, R44.2; also elsewhere on the board
VDDA: C20.2, C23.2, J3.A3, J3.B3, U11.5 (Vcc), U12.4 (V+); also elsewhere on the board

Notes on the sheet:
5v to 3.3v Opamp
Inlet Air Temperature Sensor
Battery reference voltage
Flex Sensor Input
Coolant Temperature Sensor
Throttle Position Sensor
Baro Sensor
Clutch Input
MAP Sensor
O2 Sensor

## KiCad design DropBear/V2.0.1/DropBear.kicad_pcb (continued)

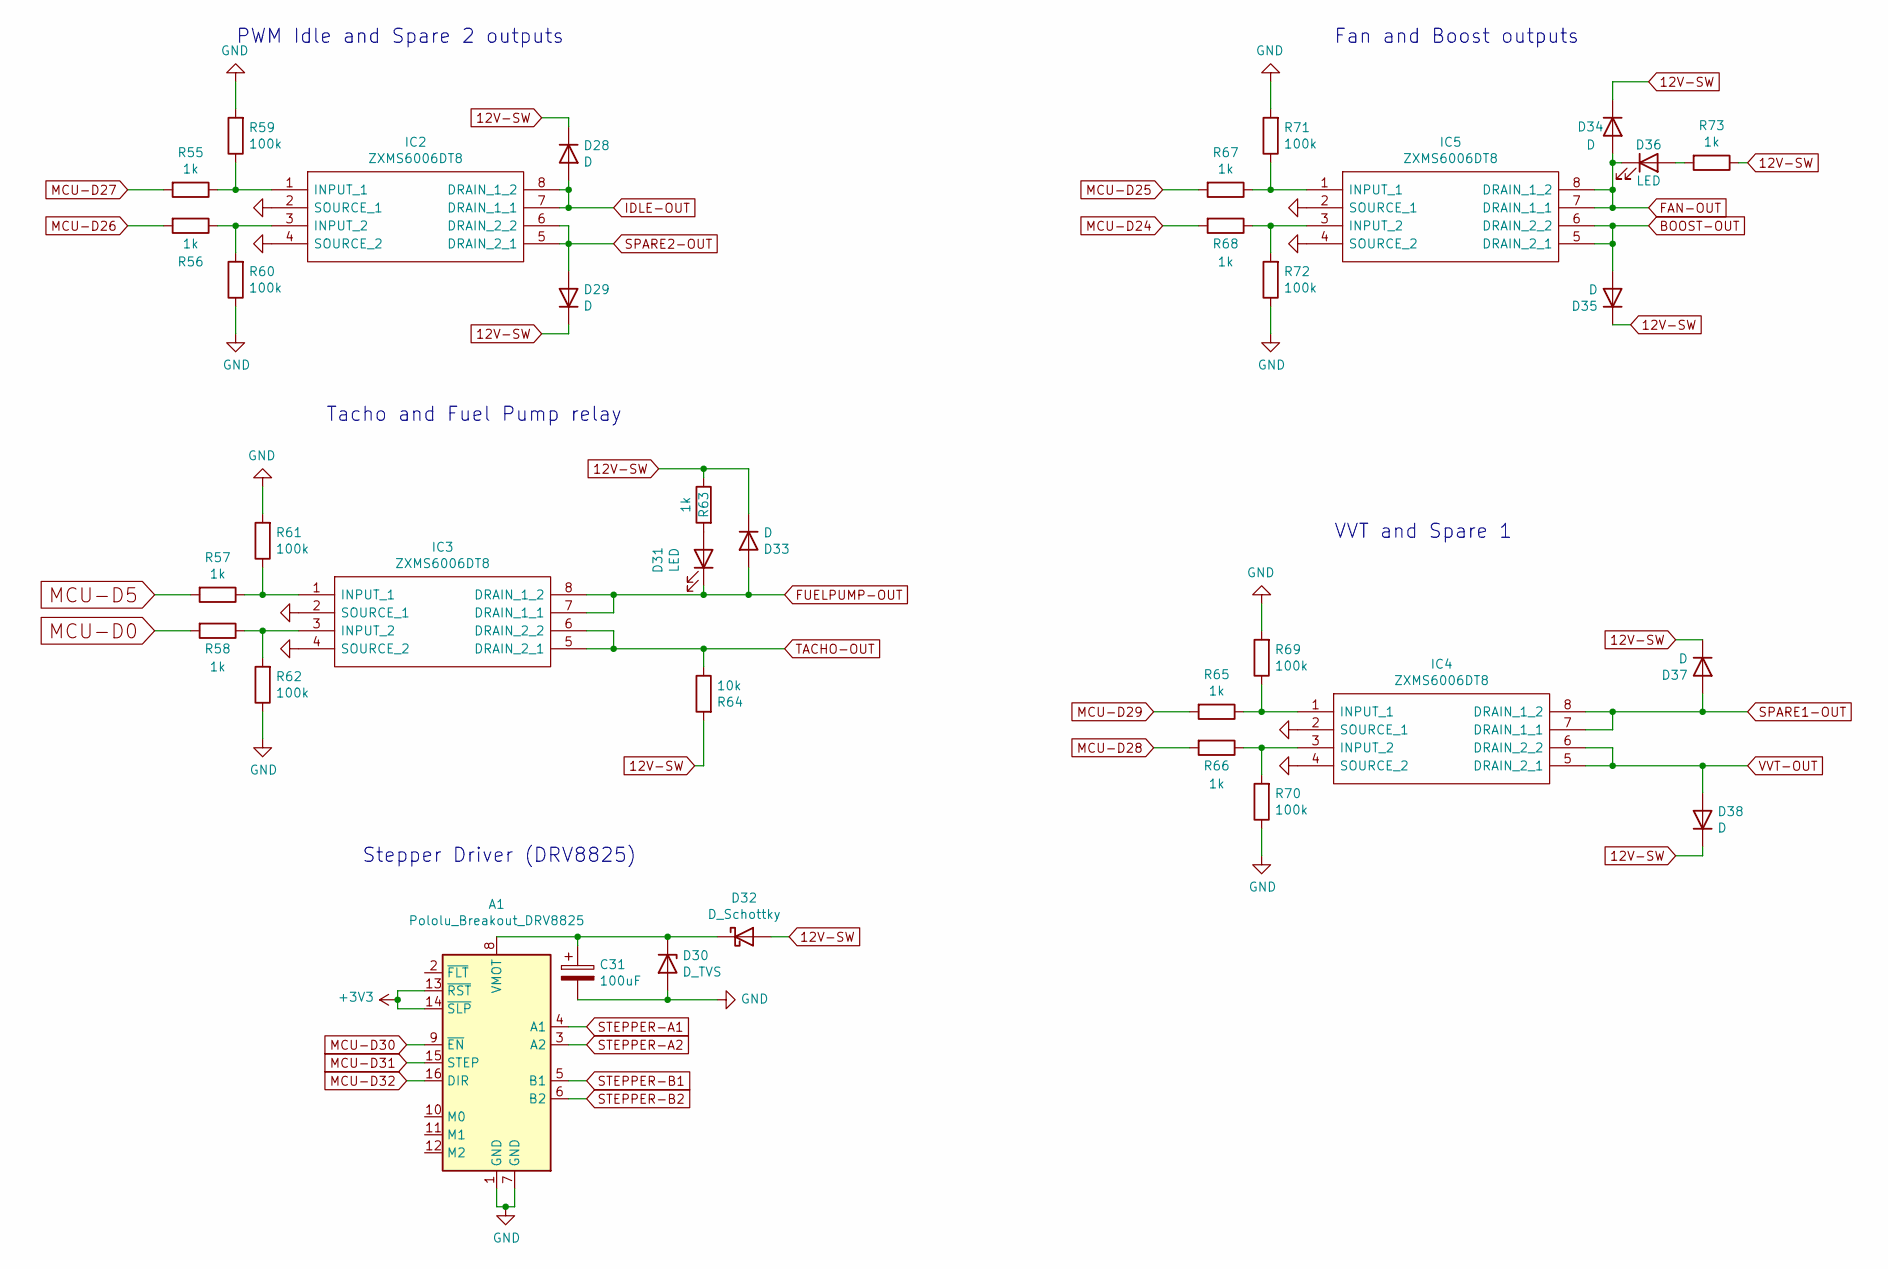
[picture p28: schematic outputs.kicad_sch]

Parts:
A1: Pololu_Breakout_DRV8825; Pololu_Breakout-16_15.2x20.3mm
C31: 100uF; CP_Elec_6.3x7.7; Manufacturer_Part_Number EEE-FT1V101AV; Digikey Part Number P124821CT-ND
D28, D29, D33, D34, D35, D37, D38: D; D_SOD-323; Manufacturer_Part_Number 1N4448WX-TP; Digikey Part Number 1N4448WXTPMSCT-ND
D30: D_TVS; D_SOD-123F; Manufacturer_Part_Number PTVS20VS1UR,115; Digikey Part Number 1727-5865-1-ND
D31: LED; LED_0805_2012Metric; Manufacturer_Part_Number LG R971-KN-1; Digikey Part Number 475-1410-2-ND
D32: D_Schottky; D_PowerDI-123; Manufacturer_Part_Number DFLS2100-7; Digikey Part Number DFLS2100-7DICT-ND
D36: LED; LED_0805_2012Metric; Manufacturer_Part_Number LH R974-LP-1; Digikey Part Number 475-1415-1-ND
IC2, IC3, IC4, IC5: ZXMS6006DT8; Diodes_SM8; Manufacturer_Part_Number ZXMS6006DT8; Digikey Part Number ZXMS6006DT8TADICT-ND
R55, R56, R57, R58, R63, R65, R66, R67, R68, R73: 1k; R_0805_2012Metric; Manufacturer_Part_Number RC0805FR-071KL; Digikey Part Number 311-1.00KCRCT-ND
R59, R60, R61, R62, R69, R70, R71, R72: 100k; R_0805_2012Metric; Manufacturer_Part_Number RC0805FR-07100KL; Digikey Part Number 311-100KCRCT-ND
R64: 10k; R_0805_2012Metric; Manufacturer_Part_Number RC0805JR-0710KL; Digikey Part Number 311-10KARCT-ND

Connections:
12V-SW: D28.1 (K), D29.1 (K), D32.2 (A), D33.1 (K), D34.1 (K), D35.1 (K), D37.1 (K), D38.1 (K), R63.1, R64.2, R73.1; also elsewhere on the board
+3V3: A1.13 (~RST), A1.14 (~SLP); also elsewhere on the board
BOOST-OUT: D35.2 (A), IC5.5 (DRAIN_2_1), IC5.6 (DRAIN_2_2); also elsewhere on the board
FAN-OUT: D34.2 (A), D36.1 (K), IC5.7 (DRAIN_1_1), IC5.8 (DRAIN_1_2); also elsewhere on the board
FUELPUMP-OUT: D31.1 (K), D33.2 (A), IC3.7 (DRAIN_1_1), IC3.8 (DRAIN_1_2); also elsewhere on the board
GND: A1.1 (GND), A1.7 (GND), C31.2, D30.2 (A), IC2.2 (SOURCE_1), IC2.4 (SOURCE_2), IC3.2 (SOURCE_1), IC3.4 (SOURCE_2), IC4.2 (SOURCE_1), IC4.4 (SOURCE_2), IC5.2 (SOURCE_1), IC5.4 (SOURCE_2), R59.2, R60.1, R61.2, R62.1, R69.2, R70.1, R71.2, R72.1; also elsewhere on the board
IDLE-OUT: A1.5 (B1), D28.2 (A), IC2.7 (DRAIN_1_1), IC2.8 (DRAIN_1_2); also elsewhere on the board
MCU-D0: R58.2; also elsewhere on the board
MCU-D5: R57.2; also elsewhere on the board
MCU-D24: R68.2; also elsewhere on the board
MCU-D25: R67.2; also elsewhere on the board
MCU-D26: R56.2; also elsewhere on the board
MCU-D27: R55.2; also elsewhere on the board
MCU-D28: R66.2; also elsewhere on the board
MCU-D29: R65.2; also elsewhere on the board
MCU-D30: A1.9 (~EN); also elsewhere on the board
MCU-D31: A1.15 (STEP); also elsewhere on the board
MCU-D32: A1.16 (DIR); also elsewhere on the board
unnamed: A1.8 (VMOT), C31.1, D30.1 (K), D32.1 (K)
unnamed: D31.2 (A), R63.2
unnamed: D36.2 (A), R73.2
unnamed: IC2.1 (INPUT_1), R55.1, R59.1
unnamed: IC2.3 (INPUT_2), R56.1, R60.2
unnamed: IC3.1 (INPUT_1), R57.1, R61.1
unnamed: IC3.3 (INPUT_2), R58.1, R62.2
unnamed: IC4.1 (INPUT_1), R65.1, R69.1
unnamed: IC4.3 (INPUT_2), R66.1, R70.2
unnamed: IC5.1 (INPUT_1), R67.1, R71.1
unnamed: IC5.3 (INPUT_2), R68.1, R72.2
SPARE1-OUT: A1.3 (A2), D37.2 (A), IC4.7 (DRAIN_1_1), IC4.8 (DRAIN_1_2); also elsewhere on the board
SPARE2-OUT: A1.6 (B2), D29.2 (A), IC2.5 (DRAIN_2_1), IC2.6 (DRAIN_2_2); also elsewhere on the board
STEPPER-A1: A1.4 (A1), D38.2 (A), IC4.5 (DRAIN_2_1), IC4.6 (DRAIN_2_2); also elsewhere on the board
TACHO-OUT: IC3.5 (DRAIN_2_1), IC3.6 (DRAIN_2_2), R64.1; also elsewhere on the board

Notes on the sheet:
Tacho and Fuel Pump relay
Fan and Boost outputs
PWM Idle and Spare 2 outputs
VVT and Spare 1
Stepper Driver (DRV8825)

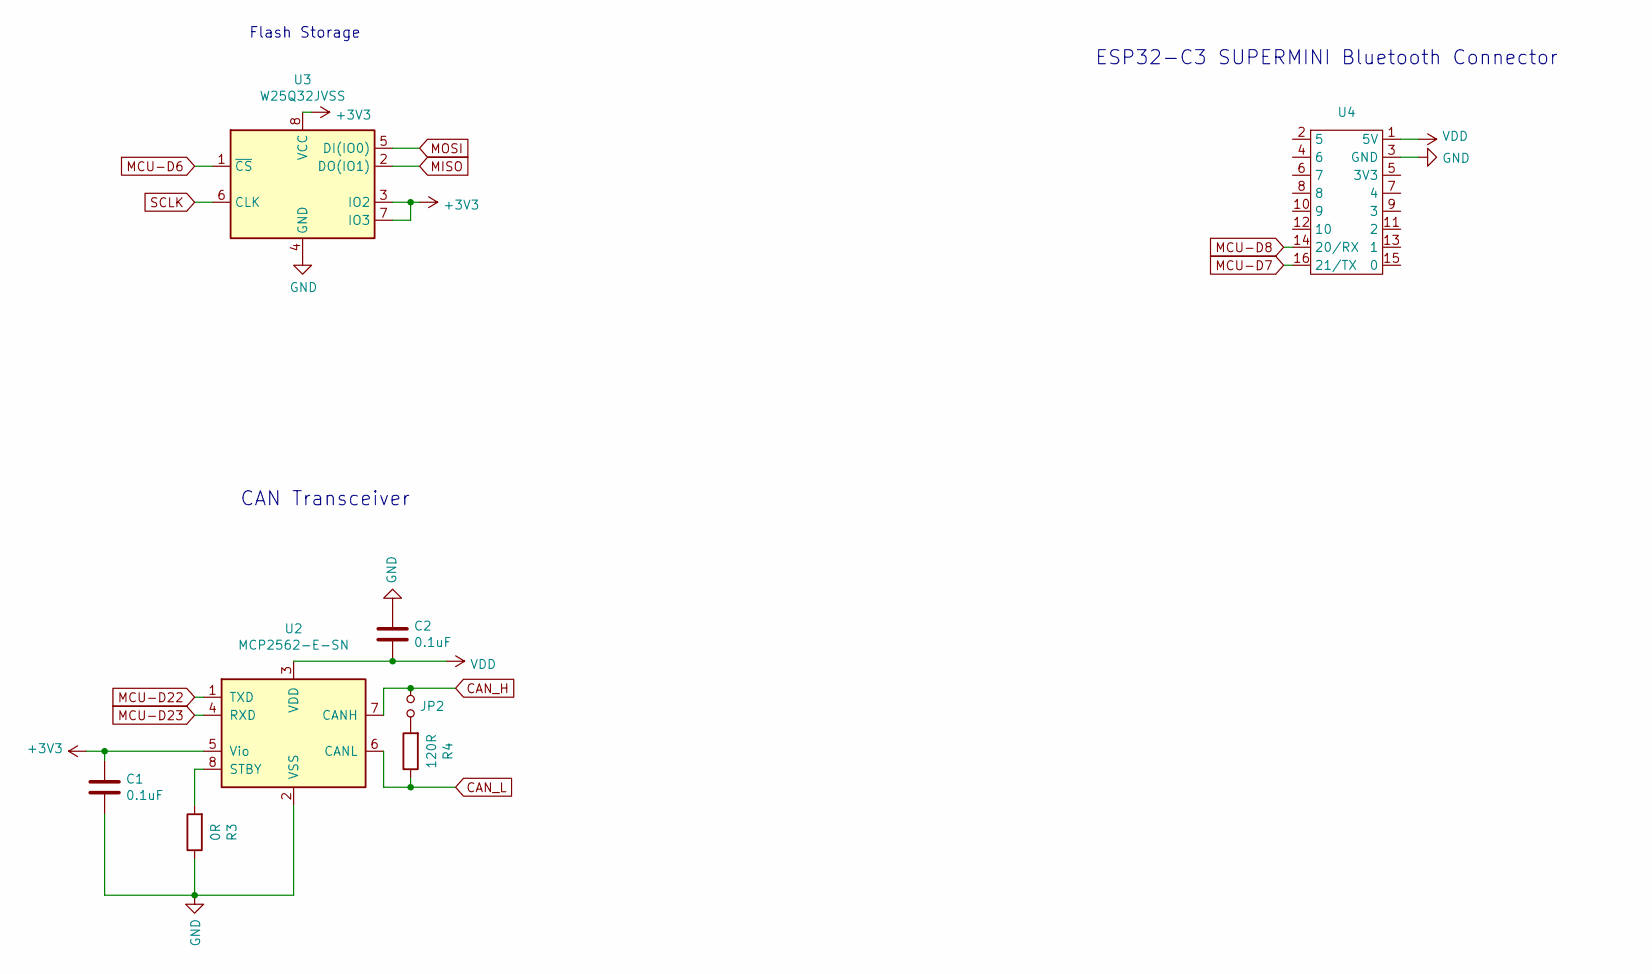
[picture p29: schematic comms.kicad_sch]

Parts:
C1, C2: 0.1uF; C_0805_2012Metric; Manufacturer_Part_Number CC0805KRX7R9BB104; Digikey Part Number 311-1140-1-ND
JP2: Jumper_NO_Small; SolderJumper-2_P1.3mm_Open_Pad1.0x1.5mm
R3: 0R; R_0805_2012Metric; Manufacturer_Part_Number RC0805JR-070RL; Digikey Part Number 311-0.0ARCT-ND
R4: 120R; R_0805_2012Metric; Manufacturer_Part_Number RC0805FR-07120RL; Digikey Part Number 311-120CRCT-ND
U2: MCP2562-E-SN; SOIC-8_3.9x4.9mm_P1.27mm; Manufacturer_Part_Number MCP2562-E/SN; Digikey Part Number MCP2562-E/SN-ND
U3: W25Q32JVSS; SOIC-8_5.23x5.23mm_P1.27mm; Manufacturer_Part_Number W25Q32JVSSIQ; Digikey Part Number W25Q32JVSSIQCT-ND
U4: ESP32-C3 SUPERMINI

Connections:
+3V3: C1.1, U2.5 (Vio), U3.3 (IO2), U3.7 (IO3), U3.8 (VCC); also elsewhere on the board
+5V: C2.2, U2.3 (VDD), U4.1 (5V); also elsewhere on the board
CAN_H: JP2.1, U2.7 (CANH); also elsewhere on the board
CAN_L: R4.1, U2.6 (CANL); also elsewhere on the board
GND: C1.2, C2.1, R3.1, U2.2 (VSS), U3.4 (GND), U4.3 (GND); also elsewhere on the board
MCU-A8: U2.1 (TXD); also elsewhere on the board
MCU-A9: U2.4 (RXD); also elsewhere on the board
MCU-D6: U3.1 (~CS); also elsewhere on the board
MCU-D7: U4.16 (21/TX); also elsewhere on the board
MCU-D8: U4.14 (20/RX); also elsewhere on the board
MISO: U3.2 (DO(IO1)); also elsewhere on the board
MOSI: U3.5 (DI(IO0)); also elsewhere on the board
unnamed: JP2.2, R4.2
unnamed: R3.2, U2.8 (STBY)
SCLK: U3.6 (CLK); also elsewhere on the board

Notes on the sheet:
Flash Storage
CAN Transceiver
ESP32-C3 SUPERMINI Bluetooth Connector

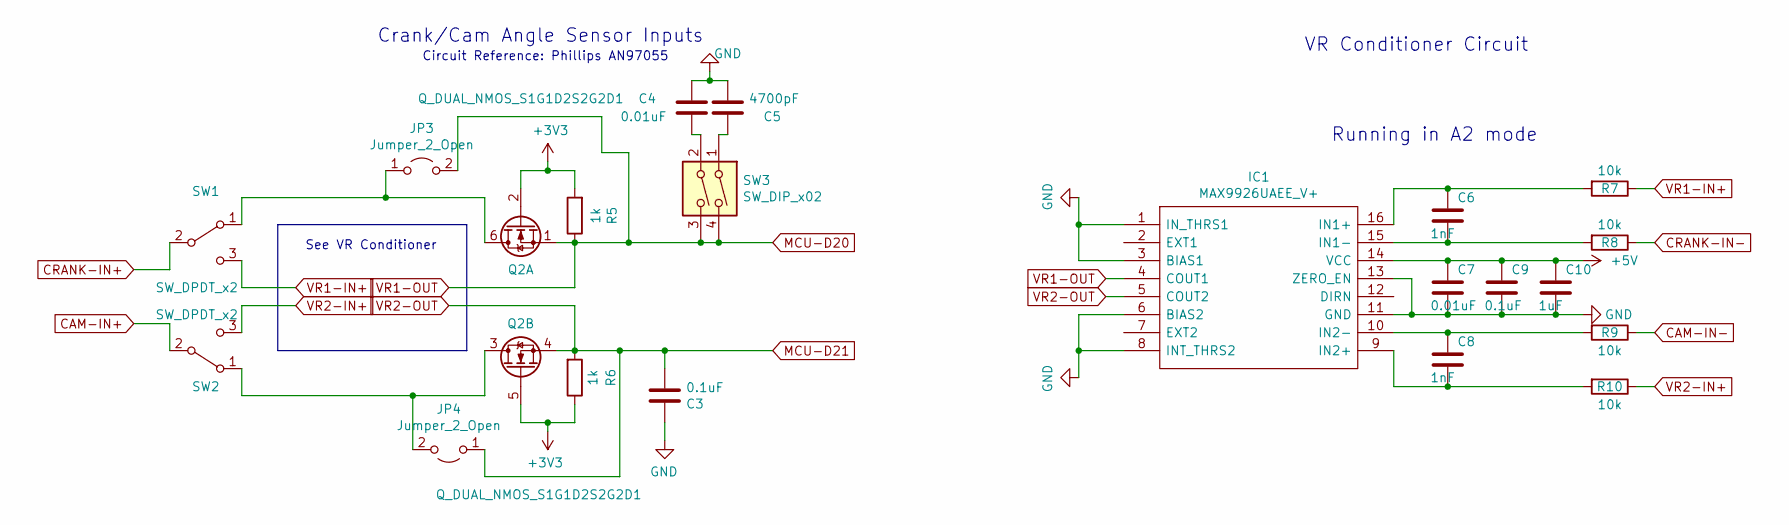
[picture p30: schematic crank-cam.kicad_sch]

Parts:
C3, C9: 0.1uF; C_0805_2012Metric; Manufacturer_Part_Number CC0805KRX7R9BB104; Digikey Part Number 311-1140-1-ND
C4, C7: 0.01uF; C_0805_2012Metric; Manufacturer_Part_Number CC0805KRX7R9BB103; Digikey Part Number 311-1136-1-ND
C5: 4700pF; C_0805_2012Metric; Manufacturer_Part_Number CC0805KRX7R9BB472; Digikey Part Number 311-1133-1-ND
C6, C8: 1nF; C_0805_2012Metric; Manufacturer_Part_Number C0805C102J5HACAUTO; Digikey Part Number 399-16591-1-ND
C10: 1uF; C_0805_2012Metric; Manufacturer_Part_Number CC0805KKX7R7BB105; Digikey Part Number 311-1365-1-ND
IC1: MAX9926UAEE_V+; QSOP-16_3.9x4.9mm_P0.635mm; Manufacturer_Part_Number MAX9926UAEE/V+; Mouser Part Number 700-MAX9926UAEE/V+
JP3, JP4: Jumper_2_Open; SolderJumper-2_P1.3mm_Open_Pad1.0x1.5mm
Q2: Q_DUAL_NMOS_S1G1D2S2G2D1; SOT-363_SC-70-6; Manufacturer_Part_Number NVJD5121NT1G; Digikey Part Number NVJD5121NT1GOSCT-ND
R5, R6: 1k; R_0805_2012Metric; Manufacturer_Part_Number RC0805FR-071KL; Digikey Part Number 311-1.00KCRCT-ND
R7, R8, R9, R10: 10k; R_1206_3216Metric; Manufacturer_Part_Number RC1206FR-7W10KL; Digikey Part Number 13-RC1206FR-7W10KLTR-ND
SW1, SW2: SW_DPDT_x2; AYZ0202AGRLC; Manufacturer_Part_Number AYZ0202AGRLC; Digikey Part Number 401-2013-1-ND
SW3: SW_DIP_x02; SW_DIP_SPSTx02_Slide_9.78x7.26mm_W8.61mm_P2.54mm; Manufacturer_Part_Number IKN0204000; Digikey Part Number 679-3566-1-ND

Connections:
+3V3: Q2.2 (G), Q2.5 (G), R5.2, R6.1; also elsewhere on the board
+5V: C7.1, C9.1, C10.1, IC1.14 (VCC); also elsewhere on the board
CAM-IN+: SW2.2 (B); also elsewhere on the board
CAM-IN-: R9.1; also elsewhere on the board
CRANK-IN+: SW1.2 (B); also elsewhere on the board
CRANK-IN-: R8.1; also elsewhere on the board
GND: C3.1, C4.1, C5.2, C7.2, C9.2, C10.2, IC1.1 (IN_THRS1), IC1.3 (BIAS1), IC1.6 (BIAS2), IC1.8 (INT_THRS2), IC1.11 (GND), IC1.13 (ZERO_EN); also elsewhere on the board
MCU-A6: IC1.4 (COUT1), JP3.2 (B), Q2.1 (S), R5.1, SW3.3, SW3.4; also elsewhere on the board
MCU-A7: C3.2, IC1.5 (COUT2), JP4.1 (A), Q2.4 (S), R6.2; also elsewhere on the board
unnamed: C4.2, SW3.2
unnamed: C5.1, SW3.1
unnamed: C6.1, IC1.16 (IN1+), R7.2
unnamed: C6.2, IC1.15 (IN1-), R8.2
unnamed: C8.2, IC1.9 (IN2+), R10.2
unnamed: C8.1, IC1.10 (IN2-), R9.2
unnamed: JP3.1 (A), Q2.6 (D), SW1.1 (A)
unnamed: JP4.2 (B), Q2.3 (D), SW2.1 (A)
VR1-IN+: R7.1, SW1.3 (C)
VR2-IN+: R10.1, SW2.3 (C)

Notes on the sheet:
Running in A2 mode
VR Conditioner Circuit
Crank/Cam Angle Sensor Inputs
See VR Conditioner
Circuit Reference: Phillips AN97055

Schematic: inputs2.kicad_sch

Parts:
C29, C30: 0.01uF; C_0805_2012Metric; Manufacturer_Part_Number CC0805KRX7R9BB103; Digikey Part Number 311-1136-1-ND
D26, D27: D_TVS; D_SOD-523; Manufacturer_Part_Number D1213A-01T-7; Digikey Part Number D1213A-01T-7DITR-ND
Q3: Q_DUAL_NMOS_S1G1D2S2G2D1; SOT-363_SC-70-6; Manufacturer_Part_Number NVJD5121NT1G; Digikey Part Number NVJD5121NT1GOSCT-ND
R49, R52: 1k; R_0805_2012Metric; Manufacturer_Part_Number RC0805FR-071KL; Digikey Part Number 311-1.00KCRCT-ND
R50, R53: 180k; R_0805_2012Metric; Manufacturer_Part_Number RC0805FR-07180KL; Digikey Part Number 311-180KCRCT-ND
R51, R54: 348k; R_0805_2012Metric; Manufacturer_Part_Number ERJ-6ENF3483V; Digikey Part Number P348KCDKR-ND
U14: LMV324LIDT; SOIC-14_3.9x8.7mm_P1.27mm; Manufacturer_Part_Number LMV324LIDT; Digikey Part Number 497-13052-1-ND

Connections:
+3V3: Q3.2 (G), Q3.5 (G), R49.2, R52.2; also elsewhere on the board
ADC-Clamp-4: U14.1, U14.2 (-); also elsewhere on the board
ADC-Clamp-10: U14.6 (-), U14.7; also elsewhere on the board
GND: C29.1, C30.1, D26.2 (A2), D27.2 (A2), R51.1, R54.1, U14.11 (V-); also elsewhere on the board
MCU-D34: C30.2, D27.1 (A1), Q3.4 (S), R52.1; also elsewhere on the board
MCU-D35: C29.2, D26.1 (A1), Q3.1 (S), R49.1; also elsewhere on the board
unnamed: R50.1, R51.2, U14.3 (+)
unnamed: R53.1, R54.2, U14.5 (+)
unnamed: U14.8, U14.9 (-)
unnamed: U14.13 (-), U14.14
SPARE1-Digital: Q3.6 (D); also elsewhere on the board
SPARE1_Sensor: R50.2; also elsewhere on the board
SPARE2-Digital: Q3.3 (D); also elsewhere on the board
SPARE2_Sensor: R53.2; also elsewhere on the board
VDDA: U14.4 (V+); also elsewhere on the board

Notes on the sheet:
5v to 3.3v Opamp
Second O2 sensor should be on Spare 2 if in use
Spare digital inputs

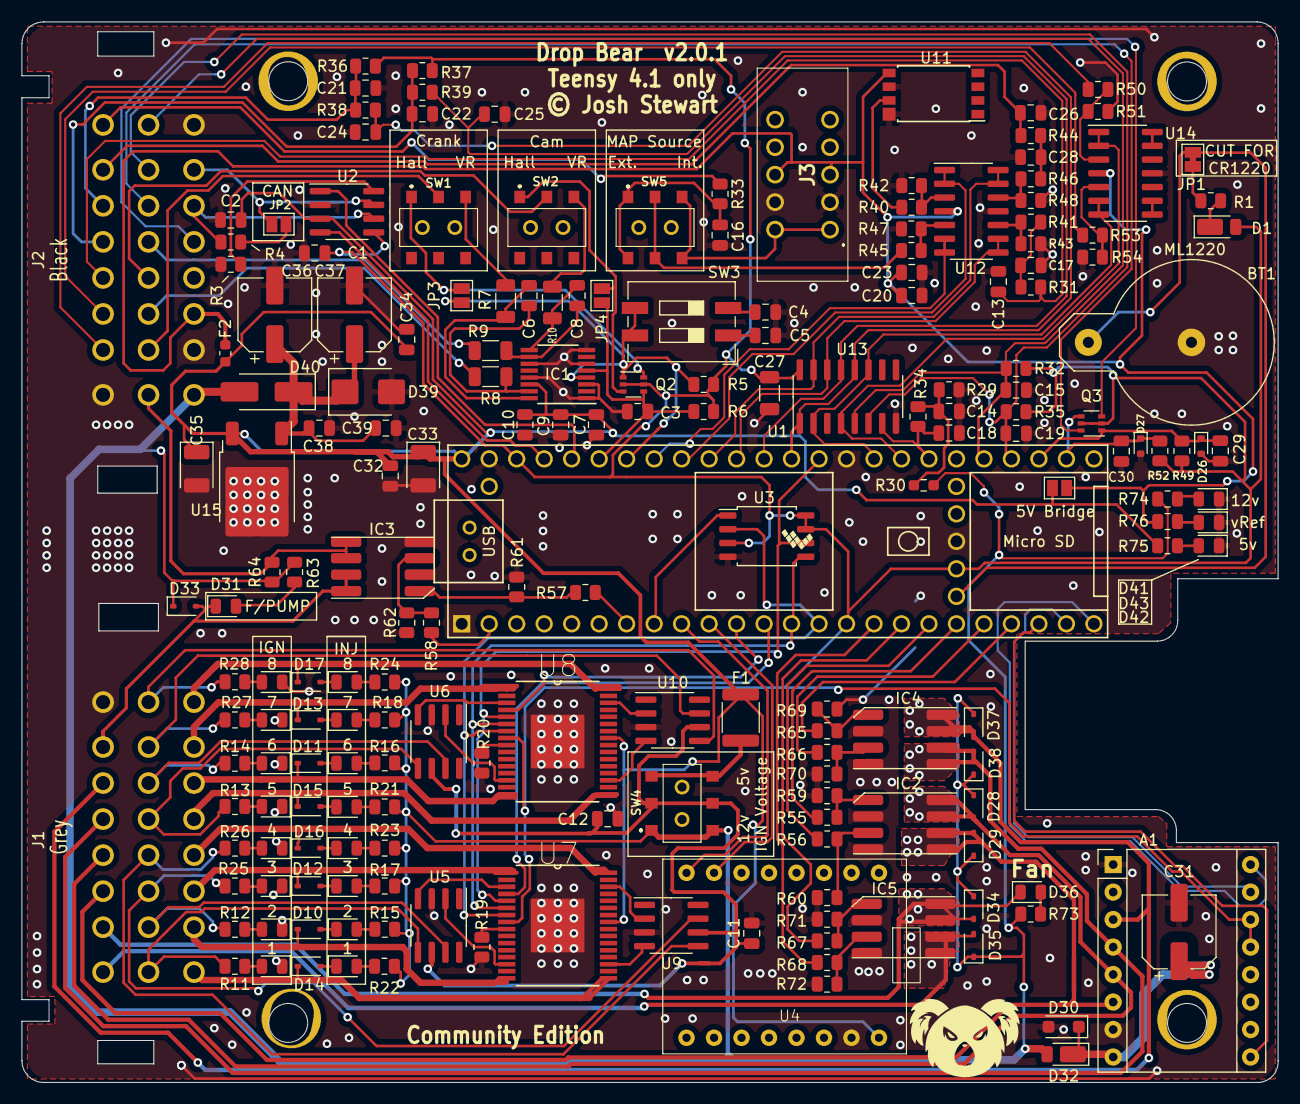
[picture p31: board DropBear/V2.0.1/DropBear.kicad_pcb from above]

Board: 2 copper layers, 116.1 x 98.0 mm, 196 parts (0 on the bottom side), 161 nets.

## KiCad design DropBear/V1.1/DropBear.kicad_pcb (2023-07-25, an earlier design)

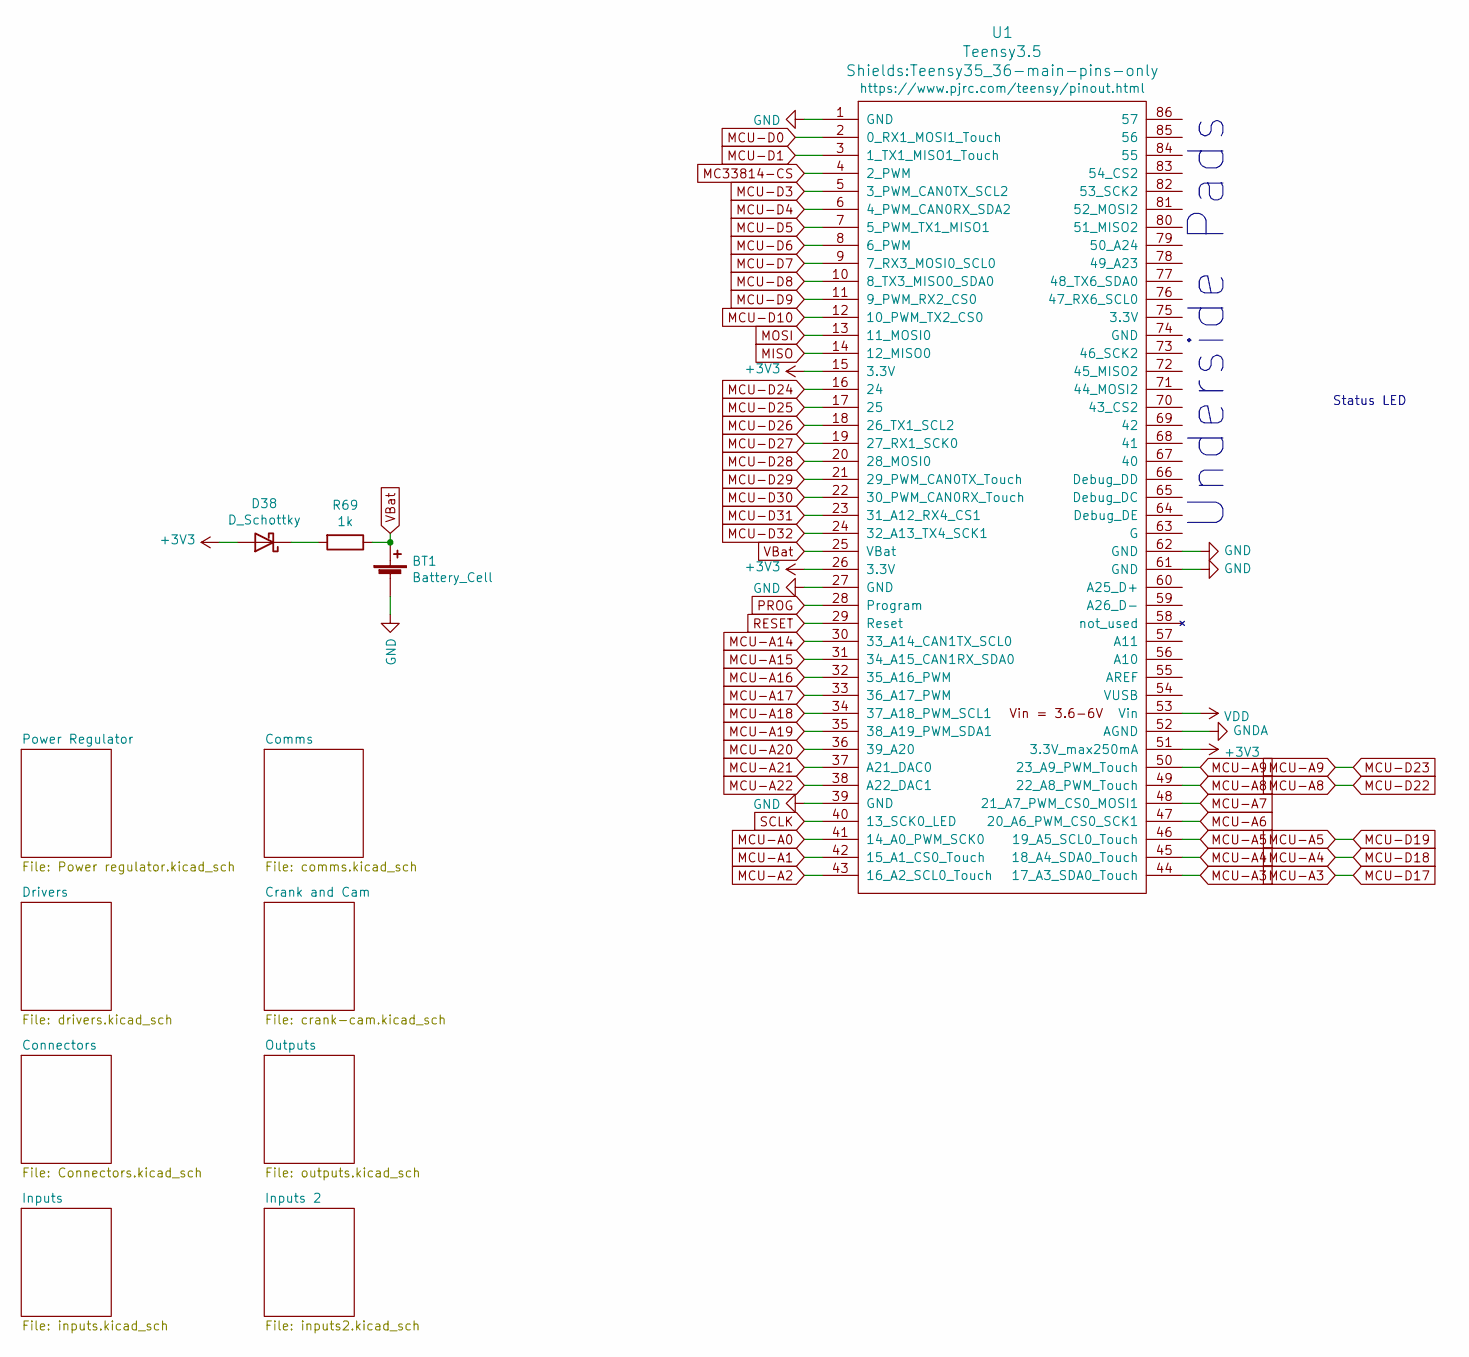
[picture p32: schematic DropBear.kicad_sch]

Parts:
BT1: Battery_Cell; 2999; Manufacturer_Part_Number 2999; Digikey Part Number 36-2999-ND
D38: D_Schottky; D_PowerDI-123; Manufacturer_Part_Number DFLS2100-7; Digikey Part Number DFLS2100-7DICT-ND
R69: 1k; R_0805_2012Metric; Manufacturer_Part_Number RC0805FR-071KL; Digikey Part Number 311-1.00KCRCT-ND
U1: Teensy3.5; Teensy35_36-main-pins-only

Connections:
+3V3: D38.2 (A), U1.15 (3.3V), U1.26 (3.3V), U1.51 (3.3V_max250mA); also elsewhere on the board
+5V: U1.53 (Vin); also elsewhere on the board
ADC-Clamp-3: U1.34 (37_A18_PWM_SCL1); also elsewhere on the board
ADC-Clamp-4: U1.33 (36_A17_PWM); also elsewhere on the board
ADC-Clamp-5: U1.32 (35_A16_PWM); also elsewhere on the board
ADC-Clamp-6: U1.31 (34_A15_CAN1RX_SDA0); also elsewhere on the board
ADC-Clamp-7: U1.30 (33_A14_CAN1TX_SCL0); also elsewhere on the board
ADC-Clamp-11: U1.35 (38_A19_PWM_SDA1); also elsewhere on the board
ADC-Clamp-12: U1.36 (39_A20); also elsewhere on the board
ADC-Clamp-13: U1.37 (A21_DAC0); also elsewhere on the board
ADC-Clamp-14: U1.38 (A22_DAC1); also elsewhere on the board
GND: BT1.2 (-), U1.1 (GND), U1.27 (GND), U1.39 (GND), U1.61 (GND), U1.62 (GND); also elsewhere on the board
GNDA: U1.52 (AGND); also elsewhere on the board
MC33810_1-CS: U1.12 (10_PWM_TX2_CS0); also elsewhere on the board
MC33810_2-CS: U1.11 (9_PWM_RX2_CS0); also elsewhere on the board
MC33814-CS: U1.4 (2_PWM); also elsewhere on the board
MCU-A0: U1.41 (14_A0_PWM_SCK0); also elsewhere on the board
MCU-A1: U1.42 (15_A1_CS0_Touch); also elsewhere on the board
MCU-A2: U1.43 (16_A2_SCL0_Touch)
MCU-A3: U1.44 (17_A3_SDA0_Touch)
MCU-A4: U1.45 (18_A4_SDA0_Touch); also elsewhere on the board
MCU-A5: U1.46 (19_A5_SCL0_Touch); also elsewhere on the board
MCU-A6: U1.47 (20_A6_PWM_CS0_SCK1)
MCU-A7: U1.48 (21_A7_PWM_CS0_MOSI1)
MCU-A8: U1.49 (22_A8_PWM_Touch); also elsewhere on the board
MCU-A9: U1.50 (23_A9_PWM_Touch); also elsewhere on the board
MCU-D0: U1.2 (0_RX1_MOSI1_Touch); also elsewhere on the board
MCU-D1: U1.3 (1_TX1_MISO1_Touch); also elsewhere on the board
MCU-D3: U1.5 (3_PWM_CAN0TX_SCL2); also elsewhere on the board
MCU-D4: U1.6 (4_PWM_CAN0RX_SDA2); also elsewhere on the board
MCU-D5: U1.7 (5_PWM_TX1_MISO1); also elsewhere on the board
MCU-D6: U1.8 (6_PWM); also elsewhere on the board
MCU-D7: U1.9 (7_RX3_MOSI0_SCL0); also elsewhere on the board
MCU-D8: U1.10 (8_TX3_MISO0_SDA0); also elsewhere on the board
MCU-D24: U1.16 (24); also elsewhere on the board
MCU-D25: U1.17 (25); also elsewhere on the board
MCU-D26: U1.18 (26_TX1_SCL2); also elsewhere on the board
MCU-D27: U1.19 (27_RX1_SCK0); also elsewhere on the board
MCU-D28: U1.20 (28_MOSI0); also elsewhere on the board
MCU-D29: U1.21 (29_PWM_CAN0TX_Touch); also elsewhere on the board
MCU-D30: U1.22 (30_PWM_CAN0RX_Touch); also elsewhere on the board
MCU-D31: U1.23 (31_A12_RX4_CS1); also elsewhere on the board
MCU-D32: U1.24 (32_A13_TX4_SCK1); also elsewhere on the board
MISO: U1.14 (12_MISO0); also elsewhere on the board
MOSI: U1.13 (11_MOSI0); also elsewhere on the board
unnamed: D38.1 (K), R69.2
PROG: U1.28 (Program)
RESET: U1.29 (Reset)
SCLK: U1.40 (13_SCK0_LED); also elsewhere on the board
VBat: BT1.1 (+), R69.1, U1.25 (VBat)

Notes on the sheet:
Underside Pads
Status LED


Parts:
C1, C2, C6, C8: 0.1uF; C_0805_2012Metric; Manufacturer_Part_Number CC0805KRX7R9BB104; Digikey Part Number 311-1140-1-ND
C3: 22uF; CP_Elec_4x5.4; Voltage 10v; Manufacturer_Part_Number PCE3882CT-ND; Digikey Part Number EEE-1CA220WR
C4, C5: 47uF; CP_EIA-3528-21_Kemet-B; Voltage 10V; Manufacturer_Part_Number TAJB476K006RNJ; Digikey Part Number 478-1692-1-ND
C7, C9: 33uF; CP_Elec_6.3x7.7; Voltage 50V; Manufacturer_Part_Number EEE-1HA330XP; Digikey Part Number PCE3925CT-ND
D10: D_TVS; D_SMB; Manufacturer_Part_Number SMBJ40A-Q; Digikey Part Number SMBJ40A-QCT-ND
D11: D_Schottky; D_SMA_Handsoldering; Manufacturer_Part_Number B360A-13-F; Digikey Part Number B360A-FDICT-ND
D12, D18, D29: LED; LED_0805_2012Metric_Pad1.15x1.40mm_HandSolder; Manufacturer_Part_Number LG R971-KN-1; Digikey Part Number 475-1410-2-ND
F1: Polyfuse; Fuse_0603_1608Metric; Manufacturer_Part_Number 0ZCM0008FF2G; Digikey Part Number 507-1817-1-ND
JP4: Jumper_2_Open; SolderJumper-2_P1.3mm_Open_Pad1.0x1.5mm
Q1: Q_PNP_BCEC; SOT-223-3_TabPin2; Manufacturer_Part_Number FZT753TA; Digikey Part Number FZT753CT-ND
R16: 1k; R_0805_2012Metric; Manufacturer_Part_Number RC0805FR-071KL; Digikey Part Number 311-1.00KCRCT-ND
R51, R52: 470R; R_0805_2012Metric; Manufacturer_Part_Number ERJ-6ENF4700V; Digikey Part Number P470CCT-ND
U2: MC33814; LQFP-48-1EP_7x7mm_P0.5mm_EP3.6x3.6mm_ThermalVias; Manufacturer_Part_Number MC33814AE
U12: TC4424A; SOIC-8_3.9x4.9mm_P1.27mm; Manufacturer_Part_Number TC4424AVOA; Digikey Part Number TC4424AVOA-ND

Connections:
12V-PROT: C7.1, C8.1, C9.1, D10.1 (K), D11.1 (K), Q1.3 (E), U2.11 (VPWR), U2.37 (KEYSW)
12V-SW: D11.2 (A), R16.1; also elsewhere on the board
+5V: C1.1, C4.1, JP4.1 (A), R51.1, U2.17 (VCC), U12.6 (VDD); also elsewhere on the board
GND: C1.2, C2.2, C3.2, C4.2, C5.2, C6.2, C7.2, C8.2, C9.2, D10.2 (A), D12.1 (K), D18.1 (K), D29.1 (K), U2.15 (GND), U2.22 (RGND2), U2.38 (INJGND2), U2.40 (RGND1), U2.42 (INJGND1), U2.49 (PADGND), U12.3 (GND); also elsewhere on the board
LAMPOUT: U2.21 (LAMPOUT)
MC33814-CS: U2.10 (CSB); also elsewhere on the board
MCU-D5: U12.2 (IN_A); also elsewhere on the board
MCU-D8: U12.4 (IN_B); also elsewhere on the board
MISO: U2.16 (SO); also elsewhere on the board
MOSI: U2.13 (SI); also elsewhere on the board
unnamed: C2.1, C5.1, F1.1, U2.20 (VPROT)
unnamed: D12.2 (A), R16.2
unnamed: D18.2 (A), R51.2
unnamed: D29.2 (A), R52.2
unnamed: U2.36 (RIN1), U12.5 (OUT_B)
unnamed: U2.35 (RIN2), U12.7 (OUT_A)
ROUT2: U2.23 (ROUT2); also elsewhere on the board
SCLK: U2.12 (SCLK); also elsewhere on the board
VDDA: F1.2, JP4.2 (B), R52.1; also elsewhere on the board
VPPREF: Q1.1 (B), U2.14 (VPPREF)
VPPSENS: C3.1, C6.1, Q1.2 (C), Q1.4 (C), U2.18 (VPPSENS)

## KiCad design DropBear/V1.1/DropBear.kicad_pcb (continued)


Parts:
C10: 1uF; C_0805_2012Metric; Manufacturer_Part_Number CC0805KKX7R7BB105; Digikey Part Number 311-1365-1-ND
C16: 0.1uF; C_0805_2012Metric; Manufacturer_Part_Number CC0805KRX7R9BB104; Digikey Part Number 311-1140-1-ND
D1, D2, D3, D4, D5, D6, D7, D8: LED; LED_0805_2012Metric; Manufacturer_Part_Number LH R974-LP-1; Digikey Part Number 475-1415-1-ND
D19, D22, D23, D24, D25, D26, D27, D28: D; D_SOD-323; Manufacturer_Part_Number 1N4448WX-TP; Digikey Part Number 1N4448WXTPMSCT-ND
D30, D31, D32, D33, D34, D35, D36, D37: LED; LED_0805_2012Metric; Manufacturer_Part_Number SML-H12D8TT86C; Digikey Part Number SML-H12D8TT86CCT-ND
F2: Polyfuse; Fuse_1812_4532Metric; Manufacturer_Part_Number 0ZCC0050FF2C; Digikey Part Number 507-1361-1-ND
R1, R2, R3, R4, R7, R8, R9, R10, R53, R62, R63, R64, R65, R66, R67, R68: 1k; R_0805_2012Metric; Manufacturer_Part_Number RC0805FR-071KL; Digikey Part Number 311-1.00KCRCT-ND
R5, R6: 10k; R_0805_2012Metric; Manufacturer_Part_Number RC0805JR-0710KL; Digikey Part Number 311-10KARCT-ND
SW5: SW_DPDT_x2; AYZ0202AGRLC; Manufacturer_Part_Number AYZ0202AGRLC; Digikey Part Number 401-2013-1-ND
U3, U4, U7, U8: TC4424A; SOIC-8_3.9x4.9mm_P1.27mm; Manufacturer_Part_Number TC4424AVOA; Digikey Part Number TC4424AVOA-ND
U5, U6: MC33810; SOIC32-P0.65-33N; Manufacturer_Part_Number MCZ33810EK

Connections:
12V-SW: R1.1, R2.1, R3.1, R4.1, R7.2, R8.2, R9.2, R10.2, SW5.1 (NC_1), SW5.4 (NC_2); also elsewhere on the board
+3V3: U5.8 (VDD), U6.8 (VDD); also elsewhere on the board
+5V: F2.2, U5.25 (VPWR), U6.25 (VPWR); also elsewhere on the board
GND: C10.2, C16.2, D30.1 (K), D31.1 (K), D32.1 (K), D33.1 (K), D34.1 (K), D35.1 (K), D36.1 (K), D37.1 (K), R5.2, R6.2, U3.3 (GND), U4.3 (GND), U5.33 (GND), U6.33 (GND), U7.3 (GND), U8.3 (GND); also elsewhere on the board
IGN1: R62.2, U3.5 (OUT_B); also elsewhere on the board
IGN2: R63.2, U3.7 (OUT_A); also elsewhere on the board
IGN3: R66.2, U7.7 (OUT_A); also elsewhere on the board
IGN4: R67.2, U7.5 (OUT_B); also elsewhere on the board
IGN5: R64.2, U4.5 (OUT_B); also elsewhere on the board
IGN6: R65.2, U4.7 (OUT_A); also elsewhere on the board
IGN7: R68.2, U8.7 (OUT_A); also elsewhere on the board
IGN8: R53.2, U8.5 (OUT_B); also elsewhere on the board
IGN_V+: C10.1, C16.1, SW5.2 (C_1), SW5.5 (C_2), U3.6 (VDD), U4.6 (VDD), U7.6 (VDD), U8.6 (VDD)
INJ1: D25.1 (K), U5.17 (OUT3); also elsewhere on the board
INJ2: D19.1 (K), U5.16 (OUT1); also elsewhere on the board
INJ3: D23.1 (K), U5.1 (OUT0); also elsewhere on the board
INJ4: D27.1 (K), U5.32 (OUT2); also elsewhere on the board
INJ5: D26.1 (K), U6.17 (OUT3); also elsewhere on the board
INJ6: D22.1 (K), U6.16 (OUT1); also elsewhere on the board
INJ7: D24.1 (K), U6.1 (OUT0); also elsewhere on the board
INJ8: D28.1 (K), U6.32 (OUT2); also elsewhere on the board
MC33810_1-CS: U5.4 (CS); also elsewhere on the board
MC33810_2-CS: U6.4 (CS); also elsewhere on the board
MISO: U5.7 (SO), U6.7 (SO); also elsewhere on the board
MOSI: U5.6 (SI), U6.6 (SI); also elsewhere on the board
unnamed: D1.1 (K), D19.2 (A)
unnamed: D1.2 (A), R1.2
unnamed: D2.1 (K), D22.2 (A)
unnamed: D2.2 (A), R2.2
unnamed: D3.2 (A), R3.2
unnamed: D4.2 (A), R4.2
unnamed: D5.2 (A), R7.1
unnamed: D6.2 (A), R8.1
unnamed: D7.2 (A), R9.1
unnamed: D8.2 (A), R10.1
unnamed: D3.1 (K), D23.2 (A)
unnamed: D4.1 (K), D24.2 (A)
unnamed: D5.1 (K), D25.2 (A)
unnamed: D6.1 (K), D26.2 (A)
unnamed: D7.1 (K), D27.2 (A)
unnamed: D8.1 (K), D28.2 (A)
unnamed: D30.2 (A), R53.1
unnamed: D31.2 (A), R62.1
unnamed: D32.2 (A), R63.1
unnamed: D33.2 (A), R64.1
unnamed: D34.2 (A), R65.1
unnamed: D35.2 (A), R66.1
unnamed: D36.2 (A), R67.1
unnamed: D37.2 (A), R68.1
unnamed: F2.1, SW5.3 (NO_1), SW5.6 (NO_2)
unnamed: U3.2 (IN_A), U5.14 (GD1)
unnamed: U3.4 (IN_B), U5.3 (GD0)
unnamed: U4.2 (IN_A), U6.14 (GD1)
unnamed: U4.4 (IN_B), U6.3 (GD0)
unnamed: U5.19 (GD3), U7.4 (IN_B)
unnamed: U5.30 (GD2), U7.2 (IN_A)
unnamed: U6.19 (GD3), U8.4 (IN_B)
unnamed: U6.30 (GD2), U8.2 (IN_A)
OUTEN_1: R5.1, U5.9 (OUTEN)
OUTEN_2: R6.1, U6.9 (OUTEN)
SCLK: U5.5 (SCLK), U6.5 (SCLK); also elsewhere on the board

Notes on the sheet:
*Note: Max current per injector channel is 3.5A


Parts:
J1: Delphi_Sicma_24; Delphi_Sicma_24_Grey
J2: Delphi_Sicma_24; Delphi_Sicma_24_Black

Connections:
12V-SW: J2.A1; also elsewhere on the board
ADC-Clamp-5: J2.B8; also elsewhere on the board
ADC-Clamp-6: J2.B7; also elsewhere on the board
BOOST-OUT: J1.C1; also elsewhere on the board
CAM-IN+: J2.B4; also elsewhere on the board
CAM-IN-: J2.B5; also elsewhere on the board
CAN_H: J2.A7; also elsewhere on the board
CAN_L: J2.A6; also elsewhere on the board
CLT_Sensor: J2.C5; also elsewhere on the board
CRANK-IN+: J2.B2; also elsewhere on the board
CRANK-IN-: J2.B3; also elsewhere on the board
FAN-OUT: J1.C2; also elsewhere on the board
GND: J1.C8, J2.A2, J2.A8; also elsewhere on the board
GNDA: J2.C1; also elsewhere on the board
IAT_Sensor: J2.C6; also elsewhere on the board
IDLE-OUT: J1.C4; also elsewhere on the board
IGN1: J1.B1; also elsewhere on the board
IGN2: J1.B2; also elsewhere on the board
IGN3: J1.B3; also elsewhere on the board
IGN4: J1.B4; also elsewhere on the board
IGN5: J1.B5; also elsewhere on the board
IGN6: J1.B6; also elsewhere on the board
IGN7: J1.B7; also elsewhere on the board
IGN8: J1.B8; also elsewhere on the board
INJ1: J1.A1; also elsewhere on the board
INJ2: J1.A2; also elsewhere on the board
INJ3: J1.A3; also elsewhere on the board
INJ4: J1.A4; also elsewhere on the board
INJ5: J1.A5; also elsewhere on the board
INJ6: J1.A6; also elsewhere on the board
INJ7: J1.A7; also elsewhere on the board
INJ8: J1.A8; also elsewhere on the board
MAP_External: J2.C8; also elsewhere on the board
O2_Sensor: J2.C4; also elsewhere on the board
ROUT2: J2.B1; also elsewhere on the board
SPARE1-Digital: J2.B6; also elsewhere on the board
SPARE1-OUT: J1.C6; also elsewhere on the board
SPARE1_Sensor: J2.C2; also elsewhere on the board
SPARE2-Digital: J2.A5; also elsewhere on the board
SPARE2-OUT: J1.C3; also elsewhere on the board
SPARE2_Sensor: J2.C3; also elsewhere on the board
STEPPER-A1: J1.C5; also elsewhere on the board
TPS_Sensor: J2.C7; also elsewhere on the board
VDDA: J2.A3; also elsewhere on the board


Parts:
C11, C12, C17, C18, C19, C27: 0.1uF; C_0805_2012Metric; Manufacturer_Part_Number CC0805KRX7R9BB104; Digikey Part Number 311-1140-1-ND
C13, C23: 270nF; C_0805_2012Metric; Manufacturer_Part_Number CC0805JRX7R7BB274; Digikey Part Number 311-4268-1-ND
C14, C15, C20, C21, C22: 0.22uF; C_0805_2012Metric; Manufacturer_Part_Number CL21B224KOCNNNC; Digikey Part Number 1276-1284-1-ND
C24: 100uF; C_1206_3216Metric; Manufacturer_Part_Number CL31A107MQHNNNE; Digikey Part Number 1276-1782-1-ND
C25: 0.01uF; C_0805_2012Metric; Manufacturer_Part_Number CC0805KRX7R9BB103; Digikey Part Number 311-1136-1-ND
C26: 1uF; C_0805_2012Metric; Manufacturer_Part_Number CC0805KKX7R7BB105; Digikey Part Number 311-1365-1-ND
J3: EBC05DRXN; Manufacturer_Part_Number EBC05DRXN; Digikey Part Number S9641-ND
R11: 604R; R_0805_2012Metric; Tolerance 1%; Manufacturer_Part_Number RC0805FR-07604RL; Digikey Part Number 311-604CRCT-ND
R12: 3.88k; R_0603_1608Metric_Pad1.05x0.95mm_HandSolder; Tolerance 1%; Manufacturer_Part_Number RT0603BRD073K88L; Digikey Part Number YAG4550CT-ND
R13, R14, R20, R21, R22: 470R; R_0805_2012Metric; Manufacturer_Part_Number ERJ-6ENF4700V; Digikey Part Number P470CCT-ND
R15: 2.4k; R_0805_2012Metric; Manufacturer_Part_Number RC0805FR-072K4L; Digikey Part Number 311-2.40KCRCT-ND
R17, R18: 2.49k; R_0805_2012Metric; Tolerance 0.1%; Manufacturer_Part_Number RT0805BRD072K49L; Digikey Part Number YAG1854CT-ND
R19: 1k; R_0805_2012Metric; Manufacturer_Part_Number RC0805FR-071KL; Digikey Part Number 311-1.00KCRCT-ND
R23, R24, R29, R46: 180k; R_0805_2012Metric; Manufacturer_Part_Number RC0805FR-07180KL; Digikey Part Number 311-180KCRCT-ND
R25, R26, R30, R47: 348k; R_0805_2012Metric; Manufacturer_Part_Number ERJ-6ENF3483V; Digikey Part Number P348KCDKR-ND
R28: 0; R_0805_2012Metric; Manufacturer_Part_Number ERJ-6GEY0R00V; Digikey Part Number P0.0ACT-ND
SW3: SW_DPDT_x2; AYZ0202AGRLC; Manufacturer_Part_Number AYZ0202AGRLC; Digikey Part Number 401-2013-1-ND
U10: SP720; SOIC-16_3.9x9.9mm_P1.27mm; Manufacturer_Part_Number SP720ABTG; Digikey Part Number F3162CT-ND
U13: LMV324LIDT; SOIC-14_3.9x8.7mm_P1.27mm; Manufacturer_Part_Number LMV324LIDT; Digikey Part Number 497-13052-1-ND
U18: KP234; Manufacturer_Part_Number KP234XTMA1; Digikey Part Number 448-KP234XTMA1CT-ND

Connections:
12V-SW: R12.2; also elsewhere on the board
+3V3: C24.2, R15.1, R17.2, R18.2, R19.2, U10.16 (V+); also elsewhere on the board
ADC-Clamp-1: U10.1 (I1)
ADC-Clamp-2: U10.2 (I2)
ADC-Clamp-3: U10.3 (I3); also elsewhere on the board
ADC-Clamp-4: U10.4 (I4); also elsewhere on the board
ADC-Clamp-5: C13.1, R15.2, U10.5 (I5); also elsewhere on the board
ADC-Clamp-6: C23.1, R19.1, U10.6 (I6); also elsewhere on the board
ADC-Clamp-7: C15.1, R14.1, U10.7 (I7); also elsewhere on the board
ADC-Clamp-8: U10.9 (I8)
ADC-Clamp-9: U10.10 (I9)
ADC-Clamp-10: U10.11 (I10)
ADC-Clamp-11: C21.1, R21.1, U10.12 (I11); also elsewhere on the board
ADC-Clamp-12: C22.1, R22.1, U10.13 (I12); also elsewhere on the board
ADC-Clamp-13: U10.14 (I13), U13.8, U13.9 (-); also elsewhere on the board
ADC-Clamp-14: U10.15 (I14), U13.13 (-), U13.14; also elsewhere on the board
BARO-5V: C27.2, R23.2, R28.2
CLT_Sensor: C19.1, R18.1, R22.2; also elsewhere on the board
GND: C11.2, C12.2, C13.2, C14.2, C15.2, C17.2, C18.2, C19.2, C20.2, C21.2, C22.2, C23.2, C24.1, C25.1, C26.1, C27.1, J3.A2, J3.B2, R11.1, R25.1, R26.1, R30.1, R47.1, U10.8 (GND), U13.11 (V-), U18.6 (GND), U18.8 (GND); also elsewhere on the board
IAT_Sensor: C18.1, R17.1, R21.2; also elsewhere on the board
MAP-5V: R29.2, SW3.2 (C_1), SW3.5 (C_2)
MAP_External: SW3.1 (NC_1), SW3.4 (NC_2); also elsewhere on the board
MCU-A0: U13.1, U13.2 (-); also elsewhere on the board
MCU-A1: U13.6 (-), U13.7; also elsewhere on the board
unnamed: C12.1, R11.2, R12.1, R14.2
unnamed: J3.A1, J3.B1, SW3.3 (NO_1), SW3.6 (NO_2)
unnamed: R23.1, R25.2, U13.3 (+)
unnamed: R24.1, R26.2, U13.10 (+)
unnamed: R28.1, U18.7 (Vout)
unnamed: R29.1, R30.2, U13.5 (+)
unnamed: R46.1, R47.2, U13.12 (+)
O2-5V: C14.1, R13.1, R24.2
O2_Sensor: C11.1, R13.2; also elsewhere on the board
TPS-5V: C20.1, R20.1, R46.2
TPS_Sensor: C17.1, R20.2; also elsewhere on the board
VDDA: C25.2, C26.2, J3.A3, J3.B3, U13.4 (V+), U18.5 (Vcc); also elsewhere on the board

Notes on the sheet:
5v to 3.3v Opamp
Inlet Air Temperature Sensor
Battery reference voltage
Flex Sensor Input
Coolant Temperature Sensor
Throttle Position Sensor
Baro Sensor
Clutch Input
MAP Sensor
O2 Sensor


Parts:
A1: Pololu_Breakout_DRV8825; Pololu_Breakout-16_15.2x20.3mm
C32: 100uF; CP_Elec_6.3x7.7; Manufacturer_Part_Number EEE-FT1V101AV; Digikey Part Number P124821CT-ND
D9: D_Schottky; D_PowerDI-123; Manufacturer_Part_Number DFLS2100-7; Digikey Part Number DFLS2100-7DICT-ND
D14, D15, D16, D17, D20, D21: D; D_SOD-323; Manufacturer_Part_Number 1N4448WX-TP; Digikey Part Number 1N4448WXTPMSCT-ND
IC2, IC3, IC4: ZXMS6006DT8; Diodes_SM8; Manufacturer_Part_Number ZXMS6006DT8; Digikey Part Number ZXMS6006DT8TADICT-ND
R31, R32, R38, R39, R40, R41: 1k; R_0805_2012Metric_Pad1.15x1.40mm_HandSolder; Manufacturer_Part_Number RC0805FR-071KL; Digikey Part Number 311-1.00KCRCT-ND
R33, R34, R42, R43, R44, R45: 100k; R_0805_2012Metric_Pad1.15x1.40mm_HandSolder; Manufacturer_Part_Number RC0805FR-07100KL; Digikey Part Number 311-100KCRCT-ND
R35: 10k; R_0805_2012Metric; Manufacturer_Part_Number RC0805JR-0710KL; Digikey Part Number 311-10KARCT-ND

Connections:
12V-SW: D9.2 (A), D14.1 (K), D15.1 (K), D16.1 (K), D17.1 (K), D20.1 (K), D21.1 (K), R35.2; also elsewhere on the board
+3V3: A1.13 (~RST), A1.14 (~SLP); also elsewhere on the board
BOOST-OUT: D20.2 (A), IC4.5 (DRAIN_2_1), IC4.6 (DRAIN_2_2); also elsewhere on the board
FAN-OUT: D16.2 (A), IC4.7 (DRAIN_1_1), IC4.8 (DRAIN_1_2); also elsewhere on the board
GND: A1.1 (GND), A1.7 (GND), C32.2, IC2.2 (SOURCE_1), IC2.4 (SOURCE_2), IC3.2 (SOURCE_1), IC3.4 (SOURCE_2), IC4.2 (SOURCE_1), IC4.4 (SOURCE_2), R33.2, R34.1, R42.2, R43.1, R44.2, R45.1; also elsewhere on the board
IDLE-OUT: A1.5 (B1), D14.2 (A), IC2.7 (DRAIN_1_1), IC2.8 (DRAIN_1_2); also elsewhere on the board
MCU-D24: R41.2; also elsewhere on the board
MCU-D25: R40.2; also elsewhere on the board
MCU-D26: R32.2; also elsewhere on the board
MCU-D27: R31.2; also elsewhere on the board
MCU-D28: R39.2; also elsewhere on the board
MCU-D29: R38.2; also elsewhere on the board
MCU-D30: A1.9 (~EN); also elsewhere on the board
MCU-D31: A1.15 (STEP); also elsewhere on the board
MCU-D32: A1.16 (DIR); also elsewhere on the board
unnamed: A1.8 (VMOT), C32.1, D9.1 (K)
unnamed: IC2.1 (INPUT_1), R31.1, R33.1
unnamed: IC2.3 (INPUT_2), R32.1, R34.2
unnamed: IC3.1 (INPUT_1), R38.1, R42.1
unnamed: IC3.3 (INPUT_2), R39.1, R43.2
unnamed: IC4.1 (INPUT_1), R40.1, R44.1
unnamed: IC4.3 (INPUT_2), R41.1, R45.2
ROUT2: R35.1; also elsewhere on the board
SPARE1-OUT: A1.3 (A2), D21.2 (A), IC3.7 (DRAIN_1_1), IC3.8 (DRAIN_1_2); also elsewhere on the board
SPARE2-OUT: A1.6 (B2), D15.2 (A), IC2.5 (DRAIN_2_1), IC2.6 (DRAIN_2_2); also elsewhere on the board
STEPPER-A1: A1.4 (A1), D17.2 (A), IC3.5 (DRAIN_2_1), IC3.6 (DRAIN_2_2); also elsewhere on the board

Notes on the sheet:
Fan and Boost outputs
Fuel pump relay
PWM Idle and Spare 2 outputs
Tacho output
VVT and Spare 1
Stepper Driver (DRV8825)


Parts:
C31, C33: 0.1uF; C_0805_2012Metric; Manufacturer_Part_Number CC0805KRX7R9BB104; Digikey Part Number 311-1140-1-ND
J4: Conn_01x04; PinHeader_1x04_P2.54mm_Vertical
JP1: Jumper_NO_Small; SolderJumper-2_P1.3mm_Open_Pad1.0x1.5mm
R50: 0R; R_0805_2012Metric_Pad1.15x1.40mm_HandSolder; Manufacturer_Part_Number RC0805JR-070RL; Digikey Part Number 311-0.0ARCT-ND
R54: 120R; R_0805_2012Metric_Pad1.15x1.40mm_HandSolder; Manufacturer_Part_Number RC0805FR-07120RL; Digikey Part Number 311-120CRCT-ND
U9: ADXL343; LGA-14_3x5mm_P0.8mm_LayoutBorder1x6y; Manufacturer_Part_Number ADXL343BCCZ-RL; Digikey Part Number ADXL343BCCZ-RLCT-ND
U11: 74AHC1G32; SOT-353_SC-70-5; Manufacturer_Part_Number SN74AHC1G32DCKR; Digikey Part Number 296-8749-1-ND
U14: W25Q32JVSS; SOIC-8_5.23x5.23mm_P1.27mm; Manufacturer_Part_Number W25Q32JVSSIQ; Digikey Part Number W25Q32JVSSIQCT-ND
U19: MCP2562-E-SN; SOIC-8_3.9x4.9mm_P1.27mm; Manufacturer_Part_Number MCP2562-E/SN; Digikey Part Number MCP2562-E/SN-ND

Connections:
+3V3: C31.1, U9.1 (Vdd_I/O), U9.6 (Vs), U11.5 (VCC), U14.3 (IO2), U14.7 (IO3), U14.8 (VCC), U19.5 (Vio); also elsewhere on the board
+5V: C33.2, J4.1, U19.3 (VDD); also elsewhere on the board
CAN_H: JP1.1, U19.7 (CANH); also elsewhere on the board
CAN_L: R54.1, U19.6 (CANL); also elsewhere on the board
GND: C31.2, C33.1, J4.2, R50.1, U9.2 (GND), U9.4 (GND), U9.5 (GND), U11.3 (GND), U14.4 (GND), U19.2 (VSS); also elsewhere on the board
MCU-D0: J4.3; also elsewhere on the board
MCU-D1: J4.4; also elsewhere on the board
MCU-D3: U19.1 (TXD); also elsewhere on the board
MCU-D4: U19.4 (RXD); also elsewhere on the board
MCU-D6: U14.1 (~CS); also elsewhere on the board
MCU-D7: U9.7 (~CS), U11.2; also elsewhere on the board
MISO: U9.12 (SDO/ADDR), U14.2 (DO(IO1)); also elsewhere on the board
MOSI: U11.1, U14.5 (DI(IO0)); also elsewhere on the board
unnamed: JP1.2, R54.2
unnamed: R50.2, U19.8 (STBY)
unnamed: U9.13 (SDA/SDI/SDIO), U11.4
SCLK: U9.14 (SCL/SCLK), U14.6 (CLK); also elsewhere on the board

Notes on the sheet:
Terminator resistor is optional and left off by default
Accelerometer
Flash Storage
CAN Transceiver
HC-05 Bluetooth Connector


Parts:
C28, C35: 0.01uF; C_0805_2012Metric; Manufacturer_Part_Number CC0805KRX7R9BB103; Digikey Part Number 311-1136-1-ND
C29, C37: 0.1uF; C_0805_2012Metric; Manufacturer_Part_Number CC0805KRX7R9BB104; Digikey Part Number 311-1140-1-ND
C30: 4700pF; C_0805_2012Metric; Manufacturer_Part_Number CC0805KRX7R9BB472; Digikey Part Number 311-1133-1-ND
C34, C36: 1nF; C_0805_2012Metric; Manufacturer_Part_Number C0805C102J5HACAUTO; Digikey Part Number 399-16591-1-ND
C38: 1uF; C_0805_2012Metric; Manufacturer_Part_Number CC0805KKX7R7BB105; Digikey Part Number 311-1365-1-ND
IC1: MAX9926UAEE_V+; QSOP-16_3.9x4.9mm_P0.635mm; Manufacturer_Part_Number MAX9926UAEE/V+; Mouser Part Number 700-MAX9926UAEE/V+
JP2, JP3: Jumper_2_Open; SolderJumper-2_P1.3mm_Open_Pad1.0x1.5mm
Q2: Q_DUAL_NMOS_S1G1D2S2G2D1; SOT-363_SC-70-6; Manufacturer_Part_Number NVJD5121NT1G; Digikey Part Number NVJD5121NT1GOSCT-ND
R27, R36, R37, R59: 10k; R_1206_3216Metric; Manufacturer_Part_Number RC1206FR-7W10KL; Digikey Part Number 13-RC1206FR-7W10KLTR-ND
R48, R49: 1k; R_0805_2012Metric; Manufacturer_Part_Number RC0805FR-071KL; Digikey Part Number 311-1.00KCRCT-ND
SW1, SW2: SW_DPDT_x2; AYZ0202AGRLC; Manufacturer_Part_Number AYZ0202AGRLC; Digikey Part Number 401-2013-1-ND
SW4: SW_DIP_x02; SW_DIP_SPSTx02_Slide_9.78x7.26mm_W8.61mm_P2.54mm; Manufacturer_Part_Number IKN0204000; Digikey Part Number 679-3566-1-ND

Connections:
+3V3: Q2.2 (G), Q2.5 (G), R48.2, R49.1; also elsewhere on the board
+5V: C35.1, C37.1, C38.1, IC1.14 (VCC); also elsewhere on the board
CAM-IN+: SW2.2 (B); also elsewhere on the board
CAM-IN-: R37.1; also elsewhere on the board
CRANK-IN+: SW1.2 (B); also elsewhere on the board
CRANK-IN-: R36.1; also elsewhere on the board
GND: C28.1, C29.1, C30.2, C35.2, C37.2, C38.2, IC1.1 (IN_THRS1), IC1.3 (BIAS1), IC1.6 (BIAS2), IC1.8 (INT_THRS2), IC1.11 (GND), IC1.13 (ZERO_EN); also elsewhere on the board
MCU-A4: C29.2, IC1.5 (COUT2), JP3.1 (A), Q2.4 (S), R49.2; also elsewhere on the board
MCU-A5: IC1.4 (COUT1), JP2.2 (B), Q2.1 (S), R48.1, SW4.3, SW4.4; also elsewhere on the board
unnamed: C28.2, SW4.2
unnamed: C30.1, SW4.1
unnamed: C34.1, IC1.16 (IN1+), R27.2
unnamed: C34.2, IC1.15 (IN1-), R36.2
unnamed: C36.1, IC1.10 (IN2-), R37.2
unnamed: C36.2, IC1.9 (IN2+), R59.2
unnamed: JP2.1 (A), Q2.6 (D), SW1.1 (A)
unnamed: JP3.2 (B), Q2.3 (D), SW2.1 (A)
VR1-IN+: R27.1, SW1.3 (C)
VR2-IN+: R59.1, SW2.3 (C)

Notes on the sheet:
Running in A2 mode
VR Conditioner Circuit
Crank/Cam Angle Sensor Inputs
See VR Conditioner
Circuit Reference: Phillips AN97055

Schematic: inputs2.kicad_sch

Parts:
C39, C40: 0.01uF; C_0805_2012Metric; Manufacturer_Part_Number CC0805KRX7R9BB103; Digikey Part Number 311-1136-1-ND
Q3: Q_DUAL_NMOS_S1G1D2S2G2D1; SOT-363_SC-70-6; Manufacturer_Part_Number NVJD5121NT1G; Digikey Part Number NVJD5121NT1GOSCT-ND
R55, R57: 180k; R_0805_2012Metric; Manufacturer_Part_Number RC0805FR-07180KL; Digikey Part Number 311-180KCRCT-ND
R56, R58: 348k; R_0805_2012Metric; Manufacturer_Part_Number ERJ-6ENF3483V; Digikey Part Number P348KCDKR-ND
R60, R61: 1k; R_0805_2012Metric; Manufacturer_Part_Number RC0805FR-071KL; Digikey Part Number 311-1.00KCRCT-ND
U20: LMV324LIDT; SOIC-14_3.9x8.7mm_P1.27mm; Manufacturer_Part_Number LMV324LIDT; Digikey Part Number 497-13052-1-ND

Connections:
+3V3: Q3.2 (G), Q3.5 (G), R60.2, R61.2; also elsewhere on the board
ADC-Clamp-3: U20.6 (-), U20.7; also elsewhere on the board
ADC-Clamp-4: U20.1, U20.2 (-); also elsewhere on the board
GND: C39.1, C40.1, R56.1, R58.1, U20.11 (V-); also elsewhere on the board
MCU-A8: C40.2, Q3.4 (S), R61.1; also elsewhere on the board
MCU-A9: C39.2, Q3.1 (S), R60.1; also elsewhere on the board
unnamed: R55.1, R56.2, U20.3 (+)
unnamed: R57.1, R58.2, U20.5 (+)
unnamed: U20.8, U20.9 (-)
unnamed: U20.13 (-), U20.14
SPARE1-Digital: Q3.6 (D); also elsewhere on the board
SPARE1_Sensor: R55.2; also elsewhere on the board
SPARE2-Digital: Q3.3 (D); also elsewhere on the board
SPARE2_Sensor: R57.2; also elsewhere on the board
VDDA: U20.4 (V+); also elsewhere on the board

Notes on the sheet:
5v to 3.3v Opamp
Second O2 sensor should be on Spare 2 if in use
Spare digital inputs

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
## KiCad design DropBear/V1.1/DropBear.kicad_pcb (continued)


Board: 2 copper layers, 116.5 x 98.0 mm, 187 parts (0 on the bottom side), 165 nets.

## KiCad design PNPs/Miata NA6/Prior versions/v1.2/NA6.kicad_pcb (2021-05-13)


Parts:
F1: Polyfuse; Fuse_0603_1608Metric; Manufacturer_Part_Number 0ZCM0008FF2G; Digikey Part Number 507-1817-1-ND
U1: MC33814; LQFP-48-1EP_7x7mm_P0.5mm_EP3.6x3.6mm_ThermalVias; Manufacturer_Part_Number MC33814
XA1: Arduino_Mega2560_Shield; Arduino_Mega2560_Shield_IO_Only

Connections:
12V-SW: U1.37 (KEYSW); also elsewhere on the board
33814-CSB: U1.10 (CSB), XA1.A6
ADC-Clamp-1: XA1.A0; also elsewhere on the board
ADC-Clamp-2: XA1.A1; also elsewhere on the board
ADC-Clamp-3: XA1.A2; also elsewhere on the board
ADC-Clamp-4: XA1.A3; also elsewhere on the board
ADC-Clamp-5: XA1.A4; also elsewhere on the board
ADC-Clamp-11: XA1.D12; also elsewhere on the board
ADC-Clamp-12: XA1.D3 (D3_INT1); also elsewhere on the board
ADC-Clamp-13: XA1.D18 (D18_TX1); also elsewhere on the board
ADC-Clamp-14: XA1.D19 (D19_RX1); also elsewhere on the board
GND: U1.15 (GND), U1.22 (RGND2), U1.38 (INJGND2), U1.40 (RGND1), U1.42 (INJGND1), U1.49 (PADGND), XA1.GND1 (GND), XA1.GND2 (GND), XA1.GND3 (GND), XA1.GND5 (GND), XA1.GND6 (GND); also elsewhere on the board
MCU-A5: XA1.A5; also elsewhere on the board
MCU-A7: XA1.A7
MCU-A8: XA1.A8; also elsewhere on the board
MCU-A9: U1.36 (RIN1), XA1.A9
MCU-A10: U1.35 (RIN2), XA1.A10
MCU-A11: XA1.A11; also elsewhere on the board
MCU-D0: XA1.D0 (D0_RX0); also elsewhere on the board
MCU-D1: XA1.D1 (D1_TX0); also elsewhere on the board
MCU-D2: XA1.D2 (D2_INT0); also elsewhere on the board
MCU-D4: XA1.D4; also elsewhere on the board
MCU-D5: XA1.D5
MCU-D6: XA1.D6
MCU-D7: XA1.D7
MCU-D8: XA1.D8; also elsewhere on the board
MCU-D9: XA1.D9; also elsewhere on the board
MCU-D10: XA1.D10; also elsewhere on the board
MCU-D11: XA1.D11; also elsewhere on the board
MCU-D13: XA1.D13
MCU-D14: XA1.D14 (D14_TX3)
MCU-D15: XA1.D15 (D15_RX3)
MCU-D16: XA1.D16 (D16_TX2)
MCU-D17: XA1.D17 (D17_RX2)
MCU-D20: XA1.D20 (D20_SDA); also elsewhere on the board
MCU-D21: XA1.D21 (D21_SCL); also elsewhere on the board
MCU-D22: XA1.D22
MCU-D23: XA1.D23; also elsewhere on the board
MCU-D24: XA1.D24
MCU-D25: XA1.D25
MCU-D26: XA1.D26
MCU-D27: XA1.D27
MCU-D28: XA1.D28
MCU-D29: XA1.D29
MCU-D30: XA1.D30
MCU-D31: XA1.D31
MCU-D32: XA1.D32; also elsewhere on the board
MCU-D33: XA1.D33; also elsewhere on the board
MCU-D34: XA1.D34
MCU-D35: XA1.D35; also elsewhere on the board
MCU-D36: XA1.D36
MCU-D37: XA1.D37; also elsewhere on the board
MCU-D38: XA1.D38
MCU-D39: XA1.D39; also elsewhere on the board
MCU-D40: XA1.D40
MCU-D41: XA1.D41; also elsewhere on the board
MCU-D42: XA1.D42
MCU-D43: XA1.D43
MCU-D44: XA1.D44
MCU-D45: XA1.D45
MCU-D46: XA1.D46
MCU-D47: XA1.D47
MCU-D48: XA1.D48
MCU-D49: XA1.D49; also elsewhere on the board
MCU-D50: U1.16 (SO), XA1.D50, XA1.MISO (SPI_MISO)
MCU-D51: U1.13 (SI), XA1.D51, XA1.MOSI (SPI_MOSI)
MCU-D52: U1.12 (SCLK), XA1.D52, XA1.SCK (SPI_SCK)
MCU-D53: XA1.D53 (D53_SS)
unnamed: F1.1, U1.20 (VPROT)
RESET: XA1.RST1 (RESET); also elsewhere on the board
ROUT1: U1.41 (ROUT1); also elsewhere on the board
ROUT2: U1.23 (ROUT2); also elsewhere on the board
VDD: U1.17 (VCC), XA1.5V1 (5V), XA1.5V3 (5V), XA1.5V4 (5V); also elsewhere on the board
VDDA: F1.2; also elsewhere on the board
VIN: XA1.VIN; also elsewhere on the board
VPPREF: U1.14 (VPPREF); also elsewhere on the board
VPPSENS: U1.18 (VPPSENS); also elsewhere on the board
VRegIn: U1.11 (VPWR); also elsewhere on the board

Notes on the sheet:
Pin Translations


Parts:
D1, D2, D3, D4, D7, D8, D11, D19: LED; LED_0805_2012Metric; Manufacturer_Part_Number LH R974-LP-1; Digikey Part Number 475-1415-1-ND
D5, D6, D9, D10: D; D_SOD-323; Manufacturer_Part_Number 1N4448WX-TP; Digikey Part Number 1N4448WXTPMSCT-ND
J6: Conn_01x02; PinHeader_1x02_P2.54mm_Vertical
R1, R2, R3, R4, R15, R16, R56, R57: 100k; R_0805_2012Metric_Pad1.15x1.40mm_HandSolder; Manufacturer_Part_Number RC0805FR-07100KL; Digikey Part Number 311-100KCRCT-ND
R5, R6, R7, R8, R17, R18, R58, R59: 1k; R_0805_2012Metric_Pad1.15x1.40mm_HandSolder; Manufacturer_Part_Number RC0805FR-071KL; Digikey Part Number 311-1.00KCRCT-ND
R9, R10, R11, R12, R19, R20, R60, R61: 2.4k; R_0805_2012Metric; Manufacturer_Part_Number RC0805FR-072K4L; Digikey Part Number 311-2.40KCRCT-ND
R13, R14, R62, R63: 10R; R_0805_2012Metric; Manufacturer_Part_Number RC0805FR-0710RL; Digikey Part Number 311-10.0CRCT-ND
U2, U4: VNLD5090; SO-8_3.9x4.9mm_P1.27mm; Manufacturer_Part_Number VNLD5090-E; Digikey Part Number 497-18682-ND
U3, U10: TC4424A; SOIC-8_3.9x4.9mm_P1.27mm; Manufacturer_Part_Number TC4424AVOA; Digikey Part Number TC4424AVOA-ND

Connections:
12V-SW: R9.2, R10.2, R19.2, R20.2; also elsewhere on the board
GND: D1.1 (K), D2.1 (K), D11.1 (K), D19.1 (K), R1.2, R2.1, R3.2, R4.1, R15.2, R16.1, R56.2, R57.1, U2.5 (SOURCE2), U2.7 (SOURCE1), U3.3 (GND), U4.5 (SOURCE2), U4.7 (SOURCE1), U10.3 (GND); also elsewhere on the board
IGN-1-OUT: R13.1; also elsewhere on the board
IGN-2-OUT: R14.1; also elsewhere on the board
IGN-3-OUT: J6.1, R62.1
IGN-4-OUT: J6.2, R63.1
INJ-1-OUT: D5.1 (K), U2.8 (DRAIN1); also elsewhere on the board
INJ-2-OUT: D6.1 (K), U2.6 (DRAIN2); also elsewhere on the board
INJ-3-OUT: D9.1 (K), U4.8 (DRAIN1); also elsewhere on the board
INJ-4-OUT: D10.1 (K), U4.6 (DRAIN2); also elsewhere on the board
MCU-D8: R16.2, R18.2; also elsewhere on the board
MCU-D9: R15.1, R17.2; also elsewhere on the board
MCU-D10: R2.2, R6.2; also elsewhere on the board
MCU-D11: R1.1, R5.2; also elsewhere on the board
MCU-D32: R56.1, R58.2; also elsewhere on the board
MCU-D33: R57.2, R59.2; also elsewhere on the board
MCU-D39: R3.1, R7.2; also elsewhere on the board
MCU-D41: R4.2, R8.2; also elsewhere on the board
unnamed: D1.2 (A), R11.2
unnamed: D2.2 (A), R12.2
unnamed: D3.1 (K), D5.2 (A)
unnamed: D3.2 (A), R9.1
unnamed: D4.1 (K), D6.2 (A)
unnamed: D4.2 (A), R10.1
unnamed: D7.1 (K), D9.2 (A)
unnamed: D7.2 (A), R19.1
unnamed: D8.2 (A), R20.1
unnamed: D8.1 (K), D10.2 (A)
unnamed: D11.2 (A), R60.2
unnamed: D19.2 (A), R61.2
unnamed: R5.1, U2.1 (IN1)
unnamed: R6.1, U2.3 (IN2)
unnamed: R7.1, U3.2 (IN_A)
unnamed: R8.1, U3.4 (IN_B)
unnamed: R11.1, R13.2, U3.7 (OUT_A)
unnamed: R12.1, R14.2, U3.5 (OUT_B)
unnamed: R17.1, U4.1 (IN1)
unnamed: R18.1, U4.3 (IN2)
unnamed: R58.1, U10.2 (IN_A)
unnamed: R59.1, U10.4 (IN_B)
unnamed: R60.1, R62.2, U10.7 (OUT_A)
unnamed: R61.1, R63.2, U10.5 (OUT_B)
VDD: U3.6 (VDD), U10.6 (VDD); also elsewhere on the board

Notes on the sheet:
Injector Driver 1
Injector Driver 2
Ignition Driver 1
Ignition Driver 2


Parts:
C1: 0.01uF; C_0805_2012Metric; Part # CC0805KRX7R9BB103; Digikey Part Number 311-1136-1-ND
C2: 1uF; C_0805_2012Metric; Part # CC0805KKX7R7BB105; Digikey Part Number 311-1365-1-ND
C3, C4, C10, C11, C15, C16: 0.1uF; C_0805_2012Metric; Manufacturer_Part_Number CC0805KRX7R9BB104; Digikey Part Number 311-1140-1-ND
C5: 0.27uF; C_0805_2012Metric; Tolerance 5%; Manufacturer_Part_Number CC0805JRX7R7BB274; Digikey Part Number 311-4268-1-ND
C6, C7, C12, C13, C14: 0.22uF; C_0805_2012Metric; Manufacturer_Part_Number CL21B224KOCNNNC; Digikey Part Number 1276-1284-1-ND
C8: 470pf; C_0805_2012Metric; Part # CC0805KRX7R9BB471; Digikey Part Number 311-1124-1-ND
C9: 0.1uF; C_0805_2012Metric; Part # CC0805KRX7R9BB104; Digikey Part Number 311-1140-1-ND
R21, R29, R33, R34: 1k; R_0805_2012Metric_Pad1.15x1.40mm_HandSolder; Manufacturer_Part_Number RC0805FR-071KL; Digikey Part Number 311-1.00KCRCT-ND
R22: 3.9k; R_0805_2012Metric; Manufacturer_Part_Number RC0805FR-073K9L; Digikey Part Number 311-3.90KCRCT-ND
R23, R24, R30, R31, R32: 470R; R_0805_2012Metric; Manufacturer_Part_Number ERJ-6ENF4700V; Digikey Part Number P470CCT-ND
R25: 2.4k; R_0805_2012Metric; Manufacturer_Part_Number RC0805FR-072K4L; Digikey Part Number 311-2.40KCRCT-ND
R26: 470R; R_0805_2012Metric; Part # ERJ-6ENF4700V; Digikey Part Number P470CCT-ND
R27, R28: 2.49k; R_0805_2012Metric; Manufacturer_Part_Number RT0805BRD072K49L; Digikey Part Number YAG1854CT-ND
R35, R36: 220R; R_0805_2012Metric_Pad1.15x1.40mm_HandSolder; Manufacturer_Part_Number RC0805FR-07220RL; Digikey Part Number 311-220CRCT-ND
U5: MPX4250; Manufacturer_Part_Number MPX4250AP; Digikey Part Number MPX4250AP-ND
U6: SP720; SOIC-16_3.9x9.9mm_P1.27mm; Manufacturer_Part_Number SP720ABTG; Digikey Part Number F3162CT-ND
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

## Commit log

2021-05-13 Initial commit of the v0.3.x boards
    [schematic v0.3.1.fzz, schematic v0.3.2.fzz, schematic v0.3.3.fzz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]
2021-05-13 Add v0.4.3d and NA6 PNP
    [Fuel_Ignition.sch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]
2021-06-05 Add most of the remaining boards
    [BOM-VR-Conditioner-MAX9926+reg.csv, BOM-VR-Conditioner-MAX9926+reg.ods, BOM-octopart-20210223_vr_conditioner_max9926_reg.csv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]
2021-06-14 Folder cleanup
    [Fuel_Ignition.sch, connector.sch, inputs.sch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]
2021-06-23 Add schematic for v0.4.3d
2021-06-23 Add v0.4.4c files
    [Bom-template-0.4.4b.xlsx, Fuel_Ignition.sch, connector.sch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]
2021-06-23 Minor fix for v0.4.4c
    [v0.4.4c.kicad_pcb]
2021-07-12 Add diagrams and PCB images for older PNP boards
    [Bom-template-MX5-PNP_ITEAD V1.0.xls, Bom-template-MX5-PNP_ITEAD V1.1.xls, speeduino pro NA6.fzz]
2023-05-12 Add v0.4.4d SMD design files
    [Bom-template-0.4.4b.xlsx, Fuel_Ignition.sch, connector.sch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]
2023-05-22 NA6 PNP v1.3 files
    [48-pin breakout-B_Cu.gbl, 48-pin breakout-B_Mask.gbs, 48-pin breakout-B_Paste.gbp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]
2023-07-24 Add Dropbear v1.1 design files
    [Connectors.kicad_sch, DropBear v1.1b.csv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]
2023-07-25 Fix for unconnected ground on 1 capacitor
    [DropBear-B_Cu.gbl, DropBear-B_Mask.gbs, DropBear-B_Paste.gbp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]
2023-07-25 Minor conversion corrections on Dropbear PCB
    [DropBear.kicad_pcb]
2023-08-01 Add PDF schematic for Dropbear
2024-10-08 Add end plates for NA6 PNP
    [MX5-PNP-Endplate.dxf, MX5-PNP-Endplate.stl]
2026-02-07 Add Dropbear v2.0.1
    [Connectors.kicad_sch, DropBear v2.0.1 BOM.csv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]
2026-02-07 V0.3 MAP card
    [MAP Card-B_Cu.gbl, MAP Card-B_Mask.gbs, MAP Card-B_Paste.gbp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]
2026-02-08 Add schematic pdf for Dropbear v2.0.1

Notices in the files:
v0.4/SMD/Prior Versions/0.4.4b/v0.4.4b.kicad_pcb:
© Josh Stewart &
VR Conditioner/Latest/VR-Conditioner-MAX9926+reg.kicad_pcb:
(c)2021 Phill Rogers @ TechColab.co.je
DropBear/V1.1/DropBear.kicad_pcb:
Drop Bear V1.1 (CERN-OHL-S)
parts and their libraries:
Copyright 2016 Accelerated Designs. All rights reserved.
